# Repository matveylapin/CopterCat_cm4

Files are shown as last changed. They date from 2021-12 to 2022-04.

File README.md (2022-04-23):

# CopterCat_cm4

Полётный контроллер для стандарта FMU-v6u. Обычно на дронах для программирования устанавливают полётный контроллер, одноплатный компьютер и иногда arduino. Почему бы не объединить это в одну плату (ну или компактный стек), это уменьшит габариты и вес. В качестве arduino мы выбрали чип ESP32, это позволит организовывать из нескольких подобных плат одну независимую сеть для коммуникации между дронами.

## Спецификация 

### FMU
* STM32H753IIK6 480Mhz Cortex-M7
* 2Mb + 256Kb FLASH
* 1Mb RAM
* ICM20602, ICM42605, BMI088, BMP388, BMM150
* Полностью совместима со стандартом FMU-v6u
### Raspberry Pi
* Поддержка платы RPi CM4 
* Слот для SD-карты
* Возможность прошивки встроенной eMMC
* CAT24C256 EEPROM
* Поддержка 2 камер(CAM0-две линия, CAM1-четыре линии)
* Поддержка USB-OTG
### ESP32
* 16MB внешней FLASH (W25Q128JVS)
* 8MB внешней PSRAM (LY68L6400SLIT)
* Встроенная антенна
* USB-TTL конвертор
### Остальное
* USB-HUB USB2514B
* USB-PD с физическим переключением
* Связь ESP32 и STM32 через UART
* 3 варианта питания
* 4 универсальных GPIO от ESP32
* USB Type-C
* Размеры 40x55 мм, плата 4 слоя
___

## Разьёмы и перемычки
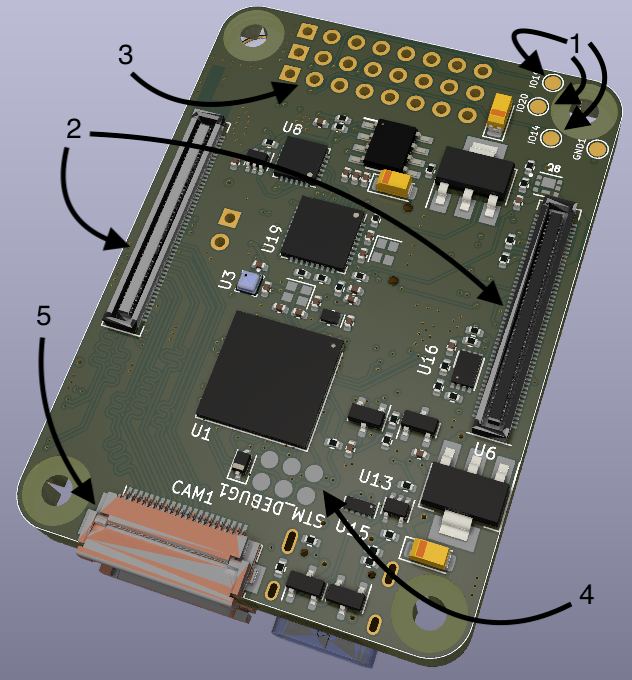
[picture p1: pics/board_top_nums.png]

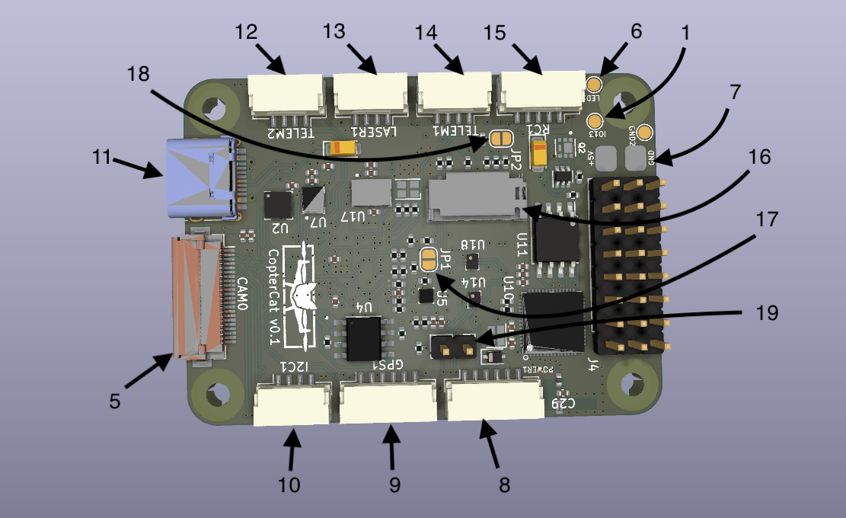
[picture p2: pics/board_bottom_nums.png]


1. GPIO ESP32 4 порта ввода вывода для подключения внешнего оборудования
2. Коннекторы RPi CM4
3. Выводы ESC 8 шт
4. Контакты программирования и отладки JTAG STM32
5. Коннекторы камер (шлейф 22 контакта с 0.5 мм расстояния между проводниками)
6. Контакт подключения адресной ленты
7. Контакты основного питания 5В
8. JST-6 стандартного шлейфа питания PX4 
9. JST-6 GPS+компас+5В
10. JST-4 I2C+5В
11. USB Type-C
12. JST-4 UART7+5В
13. JST-4 I2C RPi+3.3B для подключения дальномера
14. JST-4 UART5+5В
15. JST-5 Стандартный разъём для подключения приёмника управления
16. Слот SD карты (для RPi)
17. Джампер BOOT для STM32
18. Джампер RPIBOOT для прошивки eMMC модуля RPi CM4
19. Джампер переключения режима работы USB разъёма (при замкнутой перемычке, USB работает как вход HUB и при подключении к компьютеру будут отборажаться STM32, ESP32 и RPi CM4 в режиме OTG; при разомкнутой перемычке, USB будет работать для подключения внешних устройств к RPi, например стерео-камеры)
___

## Загрузка прошивки
### FMU
При первом запуске, в микроконтреллер придётся загрузить PX4-bootloader через порт JTAG. Подробная инструкция [здесь](https://docs.px4.io/master/en/software_update/stm32_bootloader.html#stm32-bootloader).

Для подключения к компьютеру:
1. Замкните перемычку 19
2. Подключите USB Type-C к компьютеру
3. Устройство должно появиться в [QGC](http://qgroundcontrol.com)

Также прошивку можно произвести через RPi:
1. Установите RPi CM4 в коннектор на плате
2. Разомкните перемычку 19
3. Устройство появиться в папке /dev на RPi

### ESP32
Написать программу можно либо в [Arduino IDE](https://www.arduino.cc/en/software), либо в [VS Code](https://code.visualstudio.com) с плагином [esp-idf](https://habr.com/ru/post/530638/). Далее скомпилировать и загрузить в микроконтроллер. Загрузить можно двумя способами.

С компьютера:
1. Замкните перемычку 19
2. В подключённых устройствах появиться CP2104
3. Загрузите прошивку в соотвествии с инструкцией к выбранной IDE

С RPi CM4:
1. Установите RPi CM4 в коннектор на плате
2. Разомкните перемычку 19
3. Скомпилируйте ваш код в .bin формат
4. Загрузите полученный файл на RPi
5. Загрузите прошивку в микроконтроллер с помощью esptool.py ([описание+установка](https://docs.espressif.com/projects/esptool/en/latest/esp32/index.html))

Так же ESP32 подключен к STM32 по UART, это позволит связывть между собой не просто RPi, а сразу FMU.

### RPi CM4
Слот SD карты работает как на стандартной RPi. Для плат с eMMC порядок загрузки операционной системы не отличается от CM4 IO Board ([инструкция](https://www.jeffgeerling.com/blog/2020/how-flash-raspberry-pi-os-compute-module-4-emmc-usbboot)).

___

## Общая информация
* Все требуемые для заказа файлы находится в папке /gerbers.
* Проект выполнен в программе [KiCAD v6](https://www.kicad.org)
* Библиотеки компонентов взяты с сайта [snapeda](https://www.snapeda.com)

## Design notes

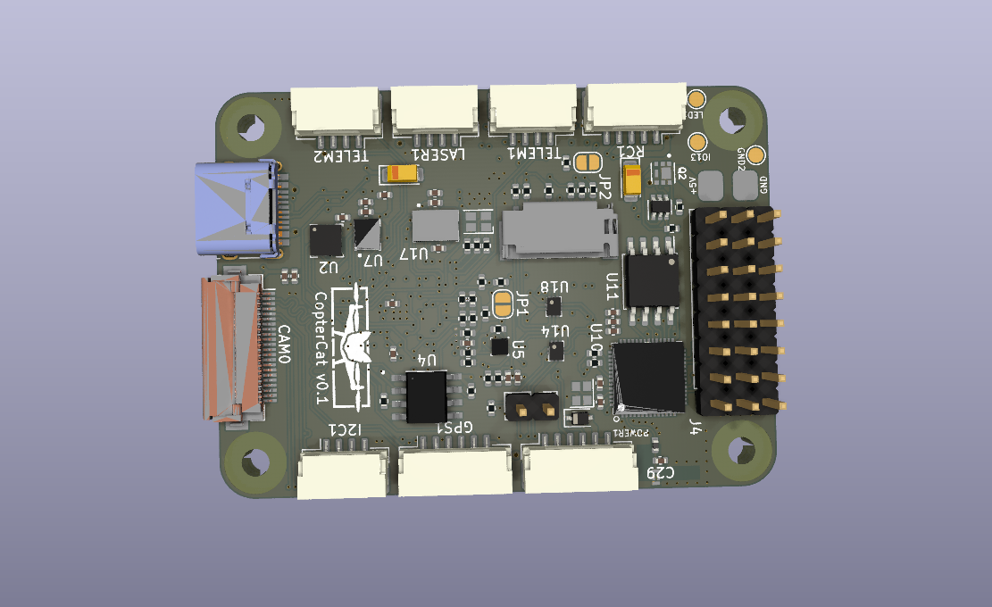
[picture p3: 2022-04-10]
pics/board_bottom.png

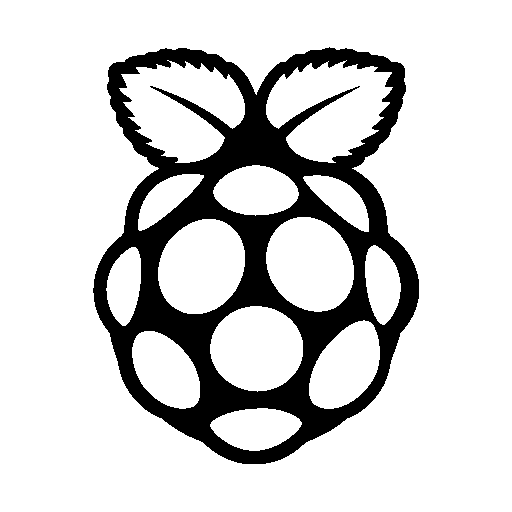
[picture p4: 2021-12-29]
pics/raspberry-pi-4-599381.bmp

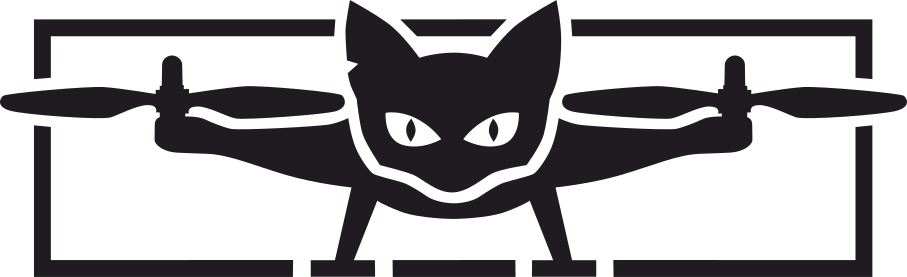
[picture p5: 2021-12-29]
pics/котокоптер лого.png

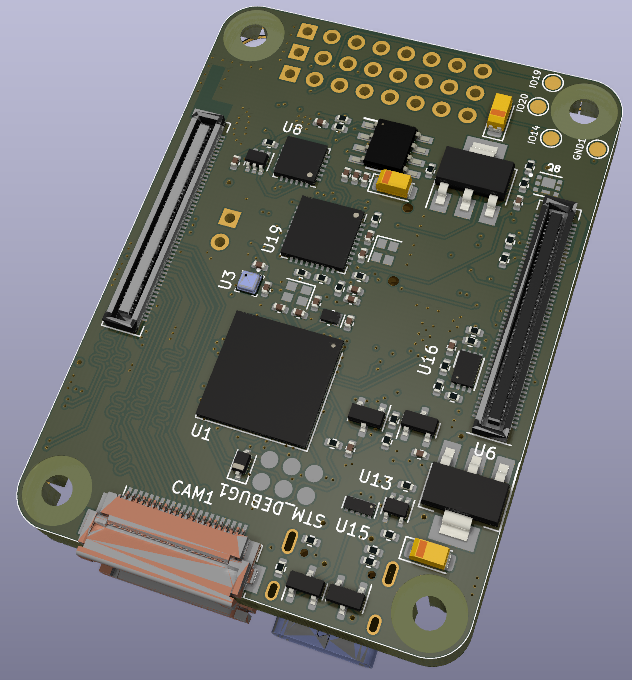
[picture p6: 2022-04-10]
pics/board_top.png

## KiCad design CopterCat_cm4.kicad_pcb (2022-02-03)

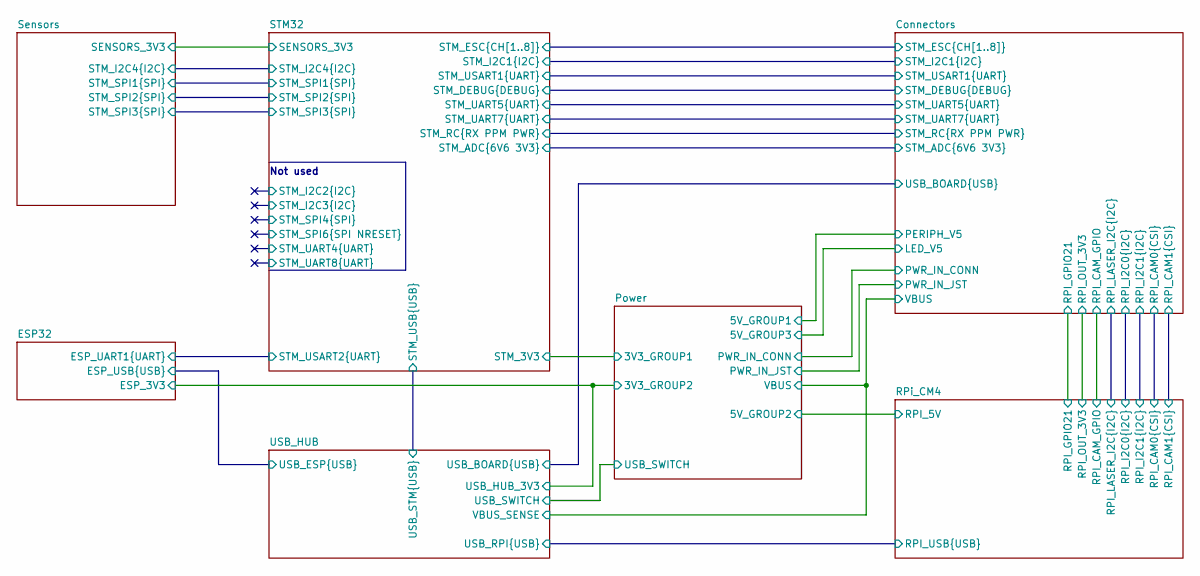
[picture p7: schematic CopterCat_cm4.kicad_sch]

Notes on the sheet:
Not used

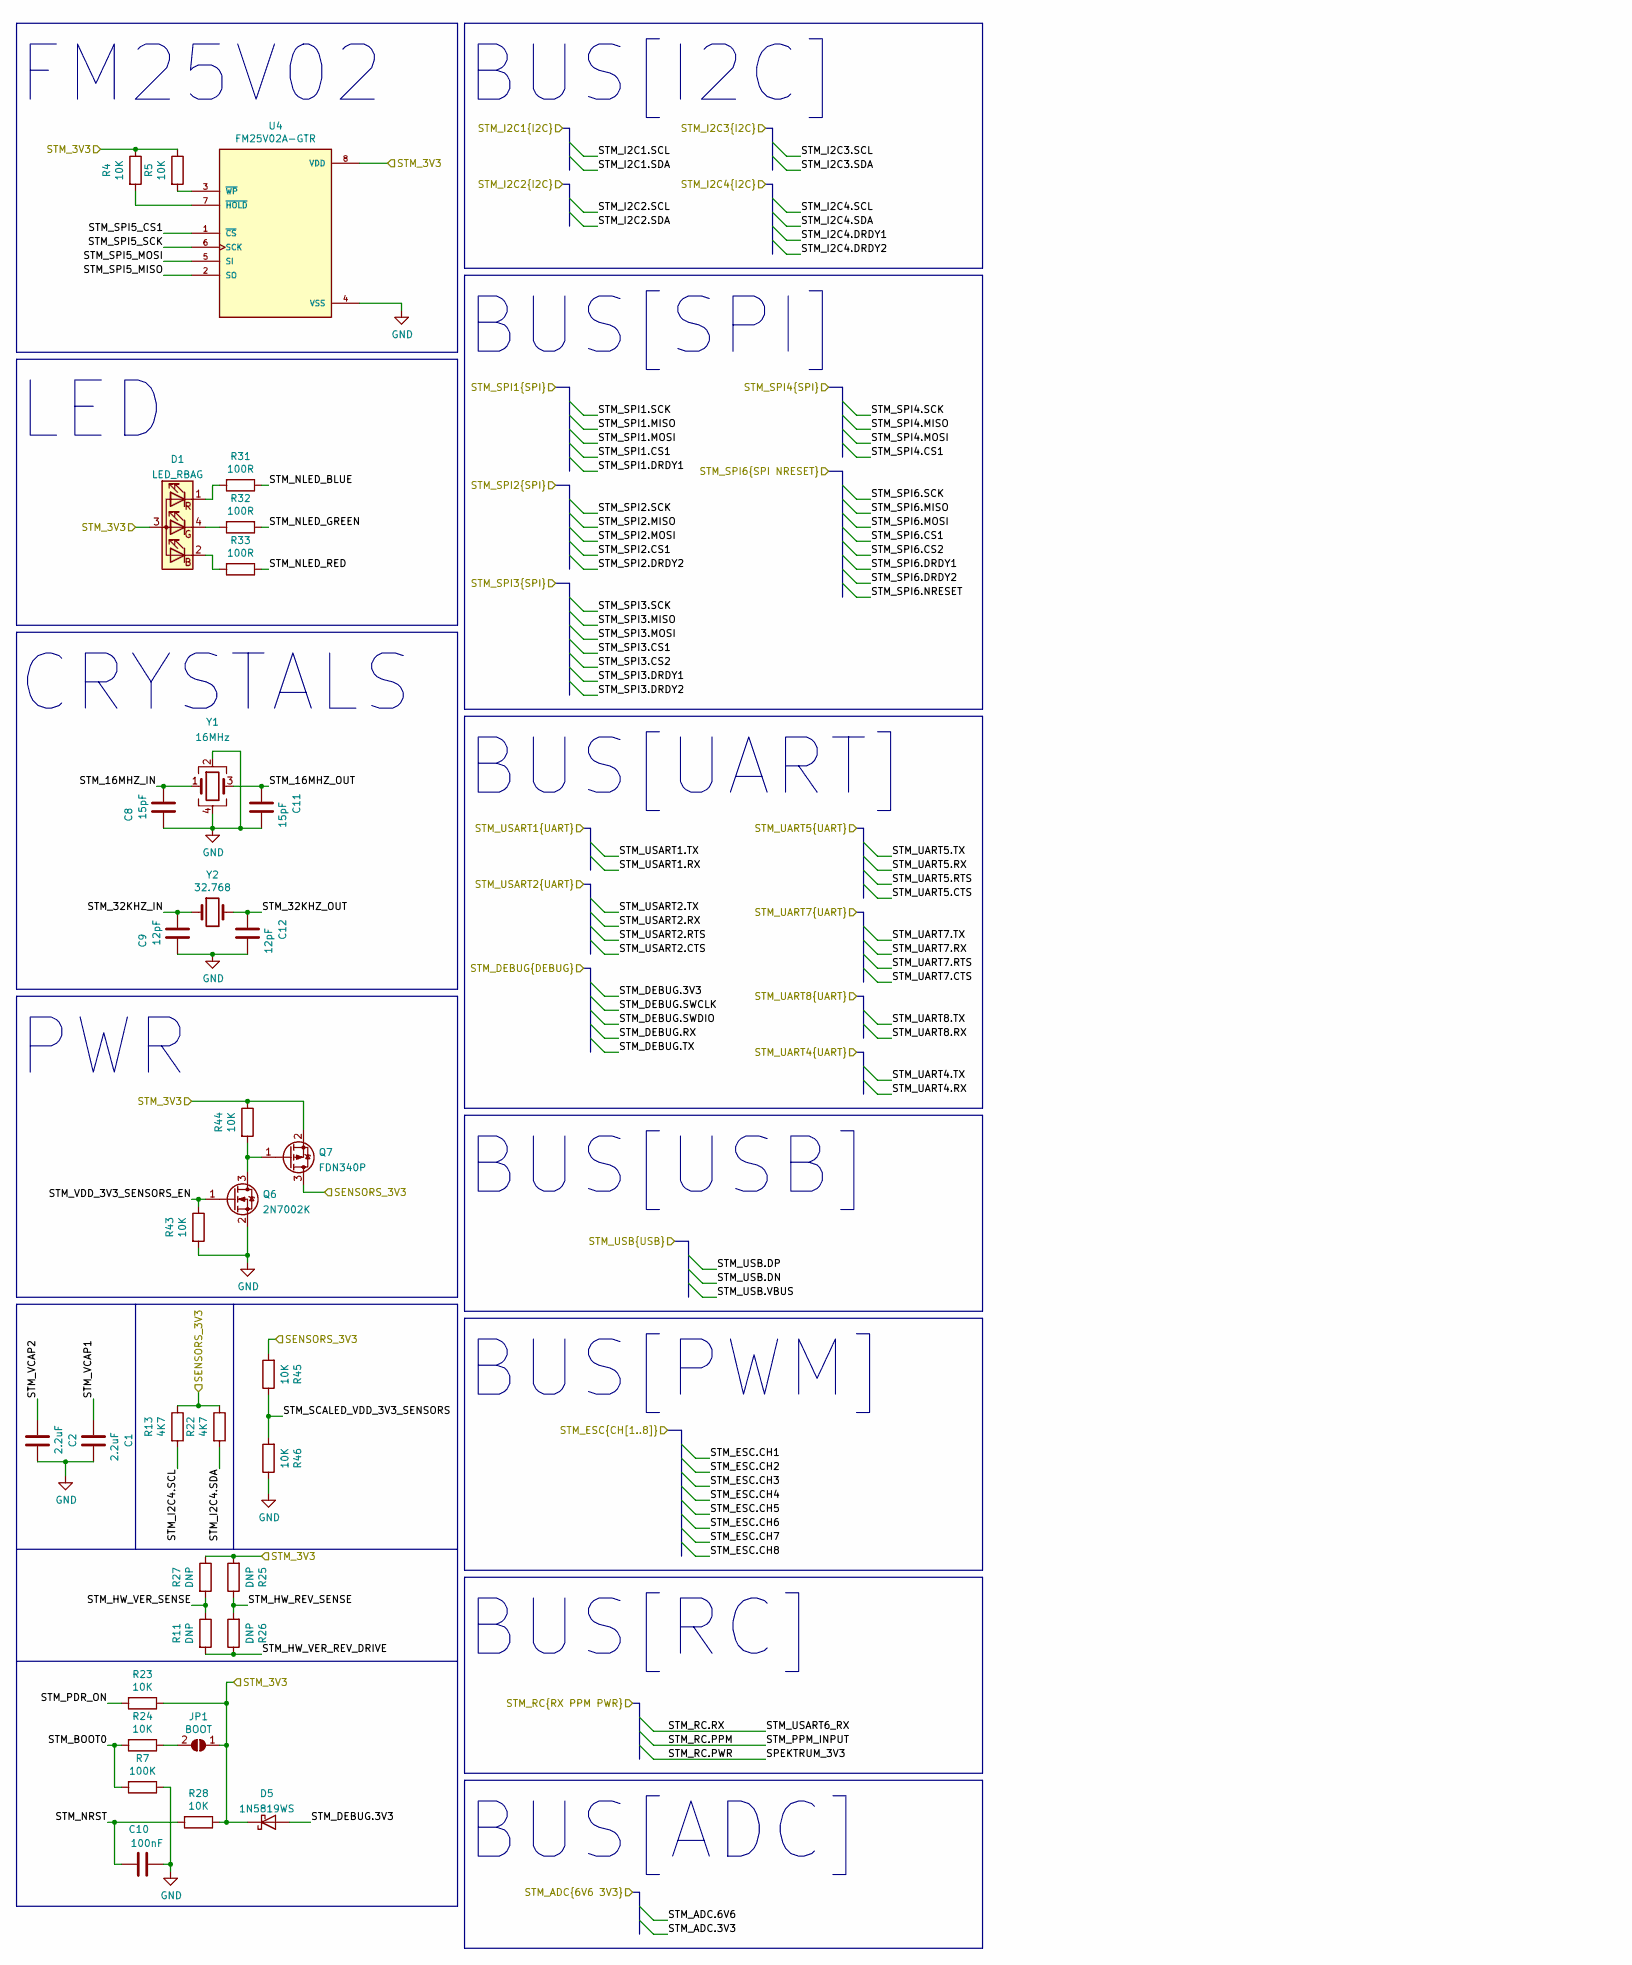
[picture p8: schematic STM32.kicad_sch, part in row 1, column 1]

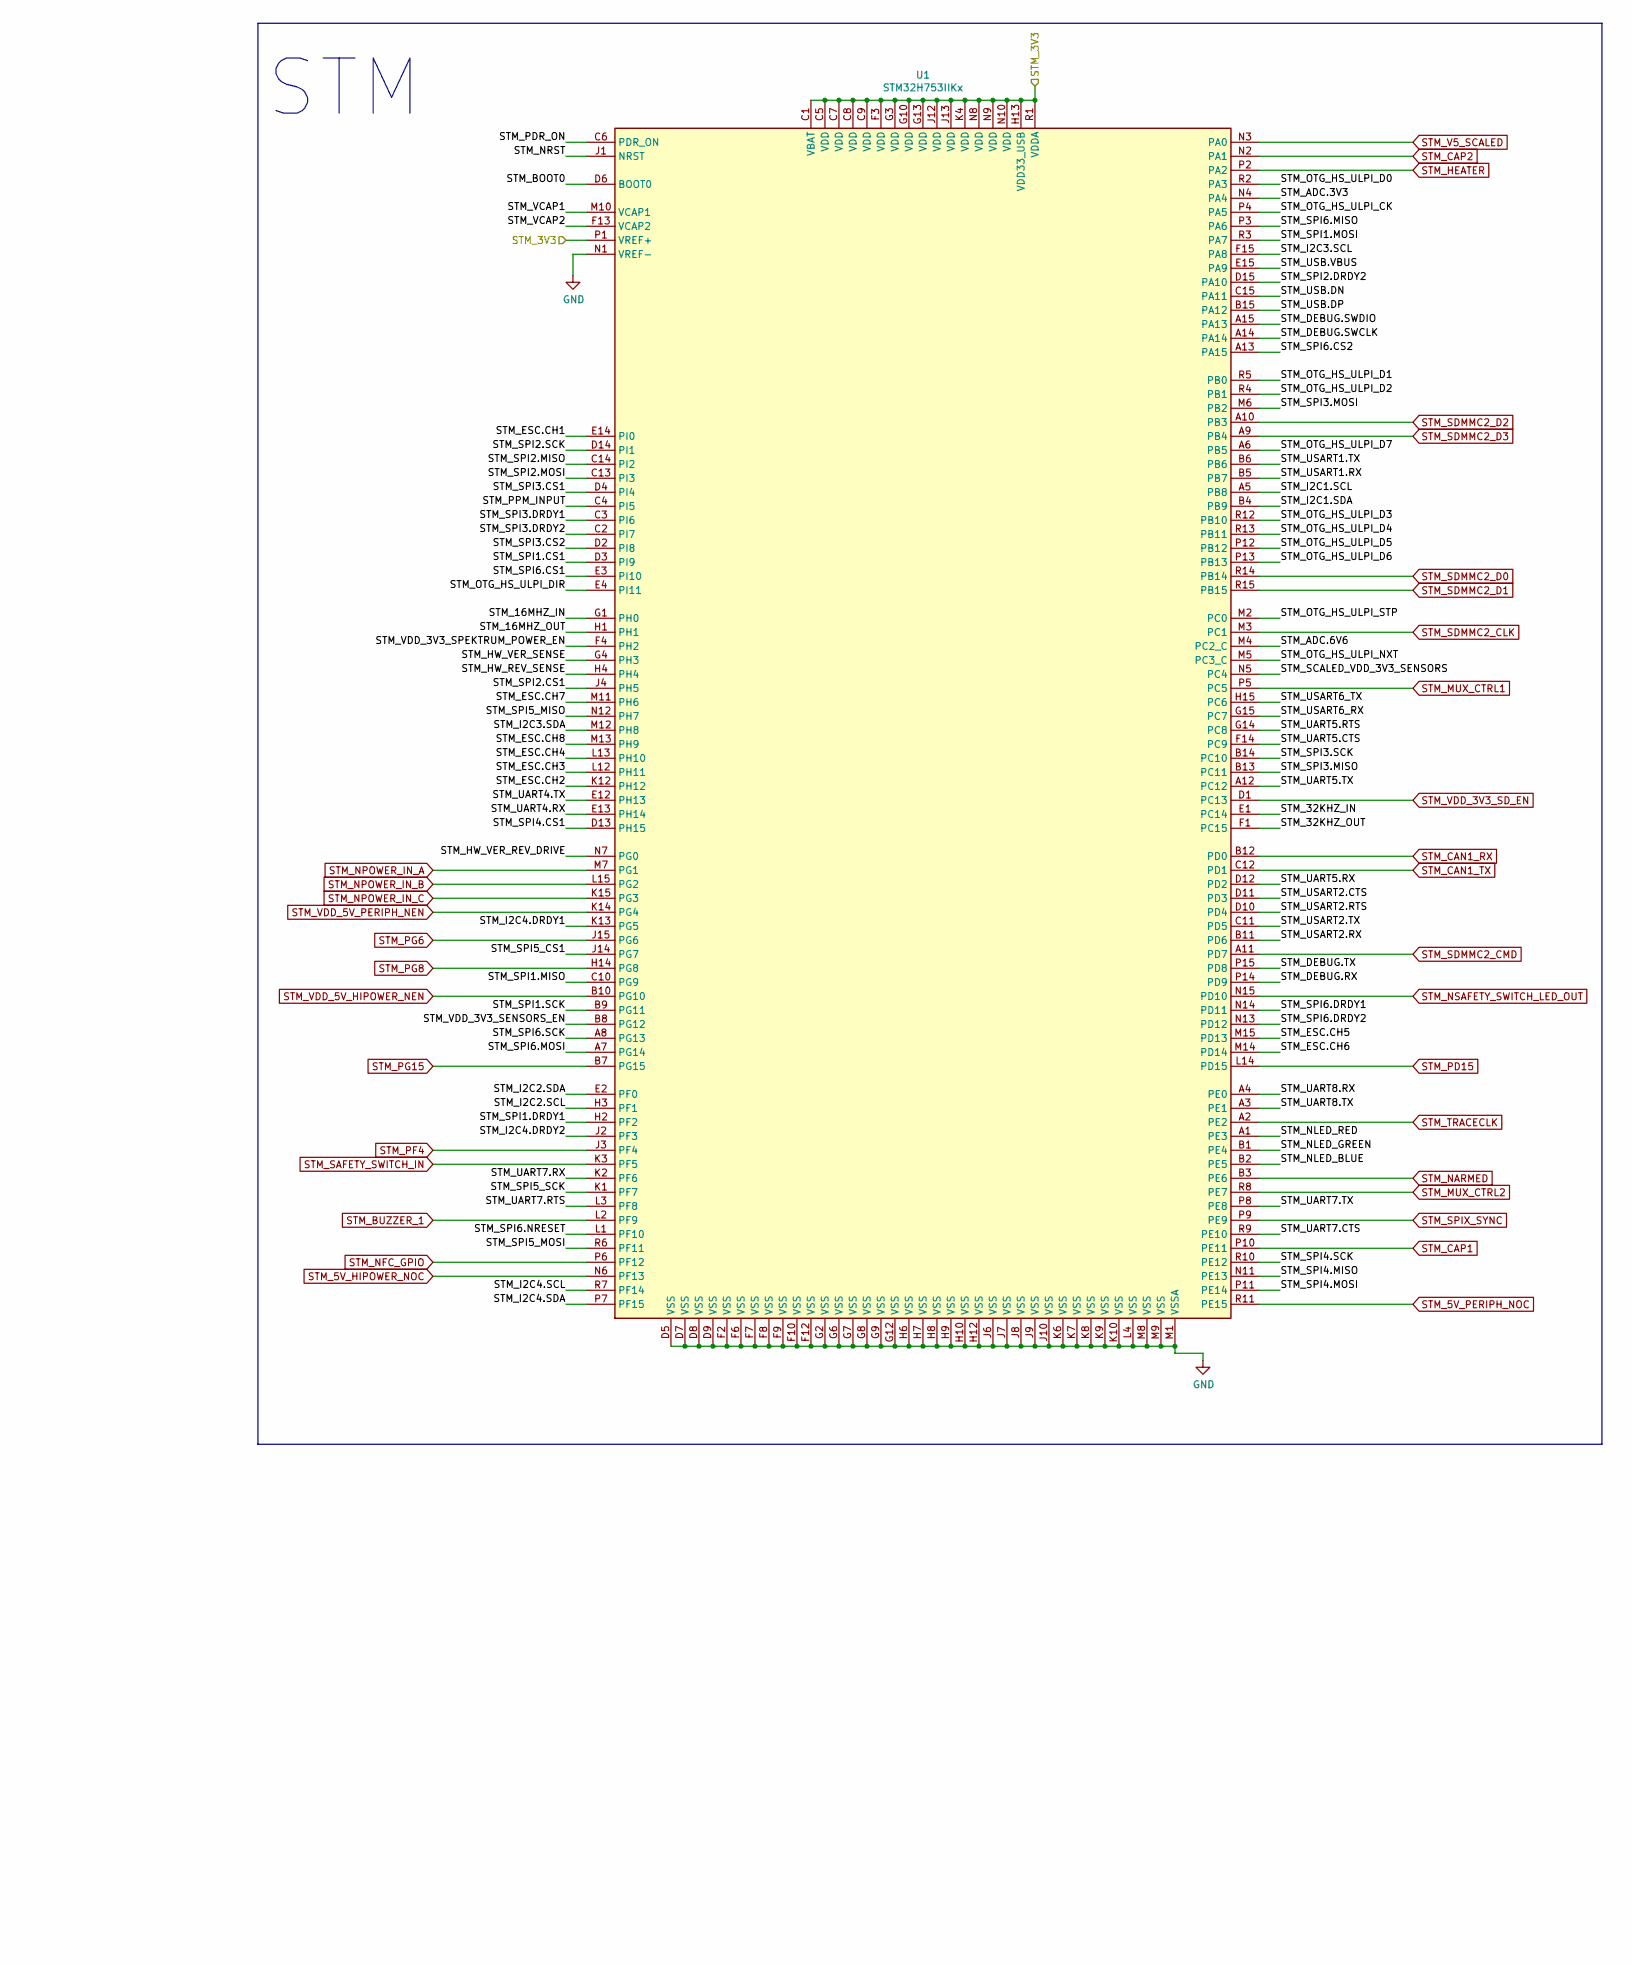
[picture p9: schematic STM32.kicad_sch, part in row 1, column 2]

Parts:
C1, C2: 2.2uF; C_0402_1005Metric
C8, C11: 15pF; C_0402_1005Metric
C9, C12: 12pF; C_0402_1005Metric
C10: 100nF; C_0402_1005Metric
D1: LED_RBAG; LED_Cree-PLCC4_2x2mm_CW; Manufacturer_Part_Number FM-B2020RGBA-HG
D5: 1N5819WS; D_SOD-323; Manufacturer_Part_Number 1N5819WS
JP1: BOOT; SolderJumper-2_P1.3mm_Open_TrianglePad1.0x1.5mm
Q6: 2N7002K; SOT-23; Manufacturer_Part_Number 2N7002,215
Q7: FDN340P; SOT-23; Manufacturer_Part_Number FDN340P
R4, R5, R23, R24, R28, R43, R44, R45, R46: 10K; R_0402_1005Metric
R7: 100K; R_0402_1005Metric
R11, R25, R26, R27: DNP; R_0402_1005Metric
R13, R22: 4K7; R_0402_1005Metric
R31, R32, R33: 100R; R_0402_1005Metric
U1: STM32H753IIKx; UFBGA-201_10x10mm_Layout15x15_P0.65mm; Manufacturer_Part_Number STM32H753IIK6
U4: FM25V02A-GTR; SOIC127P602X172-8N; Manufacturer_Part_Number FM25V02A-GTR
Y1: 16MHz; Crystal_SMD_2016-4Pin_2.0x1.6mm; Manufacturer_Part_Number OT201616MJBA4SL
Y2: 32.768; Crystal_SMD_MicroCrystal_CM9V-T1A-2Pin_1.6x1.0mm; Manufacturer_Part_Number SC-16S

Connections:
/Connectors/STM_ADC.3V3: U1.N4 (PA4); also elsewhere on the board
/Connectors/STM_ADC.6V6: U1.M4 (PC2_C); also elsewhere on the board
/Connectors/STM_DEBUG.3V3: D5.2 (A); also elsewhere on the board
/Connectors/STM_DEBUG.RX: U1.P14 (PD9); also elsewhere on the board
/Connectors/STM_DEBUG.SWCLK: U1.A14; also elsewhere on the board
/Connectors/STM_DEBUG.SWDIO: U1.A15 (PA13); also elsewhere on the board
/Connectors/STM_DEBUG.TX: U1.P15 (PD8); also elsewhere on the board
/Connectors/STM_ESC.CH1: U1.E14 (PI0); also elsewhere on the board
/Connectors/STM_ESC.CH2: U1.K12 (PH12); also elsewhere on the board
/Connectors/STM_ESC.CH3: U1.L12 (PH11); also elsewhere on the board
/Connectors/STM_ESC.CH4: U1.L13 (PH10); also elsewhere on the board
/Connectors/STM_ESC.CH5: U1.M15 (PD13); also elsewhere on the board
/Connectors/STM_ESC.CH6: U1.M14 (PD14); also elsewhere on the board
/Connectors/STM_ESC.CH7: U1.M11 (PH6); also elsewhere on the board
/Connectors/STM_ESC.CH8: U1.M13 (PH9); also elsewhere on the board
/Connectors/STM_I2C1.SCL: U1.A5 (PB8); also elsewhere on the board
/Connectors/STM_I2C1.SDA: U1.B4 (PB9); also elsewhere on the board
/Connectors/STM_RC.PPM: U1.C4 (PI5); also elsewhere on the board
/Connectors/STM_RC.RX: U1.G15 (PC7); also elsewhere on the board
/Connectors/STM_UART5.CTS: U1.F14 (PC9)
/Connectors/STM_UART5.RTS: U1.G14 (PC8)
/Connectors/STM_UART5.RX: U1.D12 (PD2); also elsewhere on the board
/Connectors/STM_UART5.TX: U1.A12 (PC12); also elsewhere on the board
/Connectors/STM_UART7.CTS: U1.R9 (PE10)
/Connectors/STM_UART7.RTS: U1.L3 (PF8)
/Connectors/STM_UART7.RX: U1.K2 (PF6); also elsewhere on the board
/Connectors/STM_UART7.TX: U1.P8 (PE8); also elsewhere on the board
/Connectors/STM_USART1.RX: U1.B5 (PB7); also elsewhere on the board
/Connectors/STM_USART1.TX: U1.B6; also elsewhere on the board
/ESP32/ESP_UART1.CTS: U1.D11 (PD3)
/ESP32/ESP_UART1.RTS: U1.D10 (PD4)
/ESP32/ESP_UART1.RX: U1.B11 (PD6); also elsewhere on the board
/ESP32/ESP_UART1.TX: U1.C11 (PD5); also elsewhere on the board
/Power/3V3_GROUP1: D1.3 (A), D5.1 (K), JP1.1 (A), Q7.2 (S), R4.1, R5.1, R23.1, R25.2, R27.1, R28.1, R44.1, U1.C1 (VBAT), U1.C5 (VDD), U1.C7 (VDD), U1.C8 (VDD), U1.C9 (VDD), U1.F3 (VDD), U1.G3 (VDD), U1.G10 (VDD), U1.G13 (VDD), U1.H13 (VDD33_USB), U1.J12 (VDD), U1.J13 (VDD), U1.K4 (VDD), U1.N8 (VDD), U1.N9 (VDD), U1.N10 (VDD), U1.P1 (VREF+), U1.R1 (VDDA), U4.8 (VDD); also elsewhere on the board
/STM32/SENSORS_3V3: Q7.3 (D), R13.1, R22.1, R45.2; also elsewhere on the board
/STM32/STM_16MHZ_IN: C8.2, U1.G1 (PH0), Y1.1
/STM32/STM_16MHZ_OUT: C11.1, U1.H1, Y1.3
/STM32/STM_32KHZ_IN: C9.2, U1.E1 (PC14), Y2.1
/STM32/STM_32KHZ_OUT: C12.1, U1.F1 (PC15), Y2.2
/STM32/STM_BOOT0: R7.2, R24.2, U1.D6 (BOOT0)
/STM32/STM_HW_REV_SENSE: R25.1, R26.2, U1.H4
/STM32/STM_HW_VER_REV_DRIVE: R11.2, R26.1, U1.N7 (PG0)
/STM32/STM_HW_VER_SENSE: R11.1, R27.2, U1.G4 (PH3)
/STM32/STM_I2C2.SCL: U1.H3 (PF1)
/STM32/STM_I2C2.SDA: U1.E2 (PF0)
/STM32/STM_I2C3.SCL: U1.F15 (PA8)
/STM32/STM_I2C3.SDA: U1.M12 (PH8)
/STM32/STM_I2C4.DRDY1: U1.K13 (PG5); also elsewhere on the board
/STM32/STM_I2C4.DRDY2: U1.J2 (PF3); also elsewhere on the board
/STM32/STM_I2C4.SCL: R13.2, U1.R7 (PF14); also elsewhere on the board
/STM32/STM_I2C4.SDA: R22.2, U1.P7 (PF15); also elsewhere on the board
/STM32/STM_NLED_BLUE: R31.1, U1.B2 (PE5)
/STM32/STM_NLED_GREEN: R32.2, U1.B1 (PE4)
/STM32/STM_NLED_RED: R33.1, U1.A1 (PE3)
/STM32/STM_NRST: C10.1, R28.2, U1.J1 (NRST)
/STM32/STM_OTG_HS_ULPI_CK: U1.P4 (PA5)
/STM32/STM_OTG_HS_ULPI_D0: U1.R2 (PA3)
/STM32/STM_OTG_HS_ULPI_D1: U1.R5 (PB0)
/STM32/STM_OTG_HS_ULPI_D2: U1.R4 (PB1)
/STM32/STM_OTG_HS_ULPI_D3: U1.R12 (PB10)
/STM32/STM_OTG_HS_ULPI_D4: U1.R13 (PB11)
/STM32/STM_OTG_HS_ULPI_D5: U1.P12 (PB12)
/STM32/STM_OTG_HS_ULPI_D6: U1.P13 (PB13)
/STM32/STM_OTG_HS_ULPI_D7: U1.A6 (PB5)
/STM32/STM_OTG_HS_ULPI_DIR: U1.E4 (PI11)
/STM32/STM_OTG_HS_ULPI_NXT: U1.M5 (PC3_C)
/STM32/STM_OTG_HS_ULPI_STP: U1.M2 (PC0)
/STM32/STM_PDR_ON: R23.2, U1.C6 (PDR_ON)
/STM32/STM_SCALED_VDD_3V3_SENSORS: R45.1, R46.2, U1.N5 (PC4)
/STM32/STM_SPI1.CS1: U1.D3 (PI9); also elsewhere on the board
/STM32/STM_SPI1.DRDY1: U1.H2 (PF2); also elsewhere on the board
/STM32/STM_SPI1.MISO: U1.C10 (PG9); also elsewhere on the board
/STM32/STM_SPI1.MOSI: U1.R3 (PA7); also elsewhere on the board
/STM32/STM_SPI1.SCK: U1.B9 (PG11); also elsewhere on the board
/STM32/STM_SPI2.CS1: U1.J4 (PH5); also elsewhere on the board
/STM32/STM_SPI2.DRDY2: U1.D15 (PA10); also elsewhere on the board
/STM32/STM_SPI2.MISO: U1.C14 (PI2); also elsewhere on the board
/STM32/STM_SPI2.MOSI: U1.C13 (PI3); also elsewhere on the board
/STM32/STM_SPI2.SCK: U1.D14 (PI1); also elsewhere on the board
/STM32/STM_SPI3.CS1: U1.D4 (PI4); also elsewhere on the board
/STM32/STM_SPI3.CS2: U1.D2 (PI8); also elsewhere on the board
/STM32/STM_SPI3.DRDY1: U1.C3 (PI6); also elsewhere on the board
/STM32/STM_SPI3.DRDY2: U1.C2 (PI7); also elsewhere on the board
/STM32/STM_SPI3.MISO: U1.B13 (PC11); also elsewhere on the board
/STM32/STM_SPI3.MOSI: U1.M6 (PB2); also elsewhere on the board
/STM32/STM_SPI3.SCK: U1.B14 (PC10); also elsewhere on the board
/STM32/STM_SPI4.CS1: U1.D13 (PH15)
/STM32/STM_SPI4.MISO: U1.N11 (PE13)
/STM32/STM_SPI4.MOSI: U1.P11 (PE14)
/STM32/STM_SPI4.SCK: U1.R10 (PE12)
/STM32/STM_SPI5_CS1: U1.J14 (PG7), U4.1 (~CS)
/STM32/STM_SPI5_MISO: U1.N12 (PH7), U4.2 (SO)
/STM32/STM_SPI5_MOSI: U1.R6 (PF11), U4.5 (SI)
/STM32/STM_SPI5_SCK: U1.K1 (PF7), U4.6 (SCK)
/STM32/STM_SPI6.CS1: U1.E3 (PI10)
/STM32/STM_SPI6.CS2: U1.A13 (PA15)
/STM32/STM_SPI6.DRDY1: U1.N14 (PD11)
/STM32/STM_SPI6.DRDY2: U1.N13 (PD12)
/STM32/STM_SPI6.MISO: U1.P3 (PA6)
/STM32/STM_SPI6.MOSI: U1.A7 (PG14)
/STM32/STM_SPI6.NRESET: U1.L1 (PF10)
/STM32/STM_SPI6.SCK: U1.A8 (PG13)
/STM32/STM_UART4.RX: U1.E13 (PH14)
/STM32/STM_UART4.TX: U1.E12 (PH13)
/STM32/STM_UART8.RX: U1.A4 (PE0)
/STM32/STM_UART8.TX: U1.A3 (PE1)
/STM32/STM_USART6_TX: U1.H15 (PC6)
/STM32/STM_USB.DN: U1.C15 (PA11); also elsewhere on the board
/STM32/STM_USB.DP: U1.B15 (PA12); also elsewhere on the board
/STM32/STM_USB.VBUS: U1.E15 (PA9); also elsewhere on the board
/STM32/STM_VCAP1: C1.1, U1.M10 (VCAP1)
/STM32/STM_VCAP2: C2.1, U1.F13 (VCAP2)
/STM32/STM_VDD_3V3_SENSORS_EN: Q6.1 (G), R43.1, U1.B8 (PG12)
/STM32/STM_VDD_3V3_SPEKTRUM_POWER_EN: U1.F4 (PH2)
GND: C1.2, C2.2, C8.1, C9.1, C10.2, C11.2, C12.2, Q6.2 (S), R7.1, R43.2, R46.1, U1.D5 (VSS), U1.D7 (VSS), U1.D8 (VSS), U1.D9 (VSS), U1.F2 (VSS), U1.F6 (VSS), U1.F7 (VSS), U1.F8 (VSS), U1.F9 (VSS), U1.F10 (VSS), U1.F12 (VSS), U1.G2 (VSS), U1.G6 (VSS), U1.G7 (VSS), U1.G8 (VSS), U1.G9 (VSS), U1.G12 (VSS), U1.H6 (VSS), U1.H7 (VSS), U1.H8 (VSS), U1.H9 (VSS), U1.H10 (VSS), U1.H12 (VSS), U1.J6 (VSS), U1.J7 (VSS), U1.J8 (VSS), U1.J9 (VSS), U1.J10 (VSS), U1.K6 (VSS), U1.K7 (VSS), U1.K8 (VSS), U1.K9 (VSS), U1.K10 (VSS), U1.L4 (VSS), U1.M1 (VSSA), U1.M8 (VSS), U1.M9 (VSS), U1.N1 (VREF-), U4.4 (VSS), Y1.2, Y1.4; also elsewhere on the board
unnamed: D1.1 (RK), R31.2
unnamed: D1.2 (BK), R33.2
unnamed: D1.4 (GK), R32.1
unnamed: JP1.2 (B), R24.1
unnamed: Q6.3 (D), Q7.1 (G), R44.2
unnamed: R4.2, U4.7 (~HOLD)
unnamed: R5.2, U4.3 (~WP)
STM_5V_HIPOWER_NOC: U1.N6 (PF13)
STM_5V_PERIPH_NOC: U1.R11 (PE15)
STM_BUZZER_1: U1.L2 (PF9)
STM_CAN1_RX: U1.B12 (PD0)
STM_CAN1_TX: U1.C12 (PD1)
STM_CAP1: U1.P10 (PE11)
STM_CAP2: U1.N2 (PA1)
STM_HEATER: U1.P2 (PA2)
STM_MUX_CTRL1: U1.P5 (PC5)
STM_MUX_CTRL2: U1.R8 (PE7)
STM_NARMED: U1.B3 (PE6)
STM_NFC_GPIO: U1.P6 (PF12)
STM_NPOWER_IN_A: U1.M7 (PG1)
STM_NPOWER_IN_B: U1.L15 (PG2)
STM_NPOWER_IN_C: U1.K15 (PG3)
STM_NSAFETY_SWITCH_LED_OUT: U1.N15 (PD10)
STM_PD15: U1.L14 (PD15)
STM_PF4: U1.J3 (PF4)
STM_PG6: U1.J15 (PG6)
STM_PG8: U1.H14 (PG8)
STM_PG15: U1.B7 (PG15)
STM_SAFETY_SWITCH_IN: U1.K3 (PF5)
STM_SDMMC2_CLK: U1.M3 (PC1)
STM_SDMMC2_CMD: U1.A11 (PD7)
STM_SDMMC2_D0: U1.R14 (PB14)
STM_SDMMC2_D1: U1.R15 (PB15)
STM_SDMMC2_D2: U1.A10 (PB3)
STM_SDMMC2_D3: U1.A9 (PB4)
STM_SPIX_SYNC: U1.P9 (PE9)
STM_TRACECLK: U1.A2 (PE2)
STM_V5_SCALED: U1.N3 (PA0)
STM_VDD_3V3_SD_EN: U1.D1 (PC13)
STM_VDD_5V_HIPOWER_NEN: U1.B10 (PG10)
STM_VDD_5V_PERIPH_NEN: U1.K14 (PG4)

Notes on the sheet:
BUS[RC]
BUS[SPI]
PWR
BUS[UART]
CRYSTALS
FM25V02
BUS[USB]
STM
BUS[ADC]
LED
BUS[PWM]
BUS[I2C]

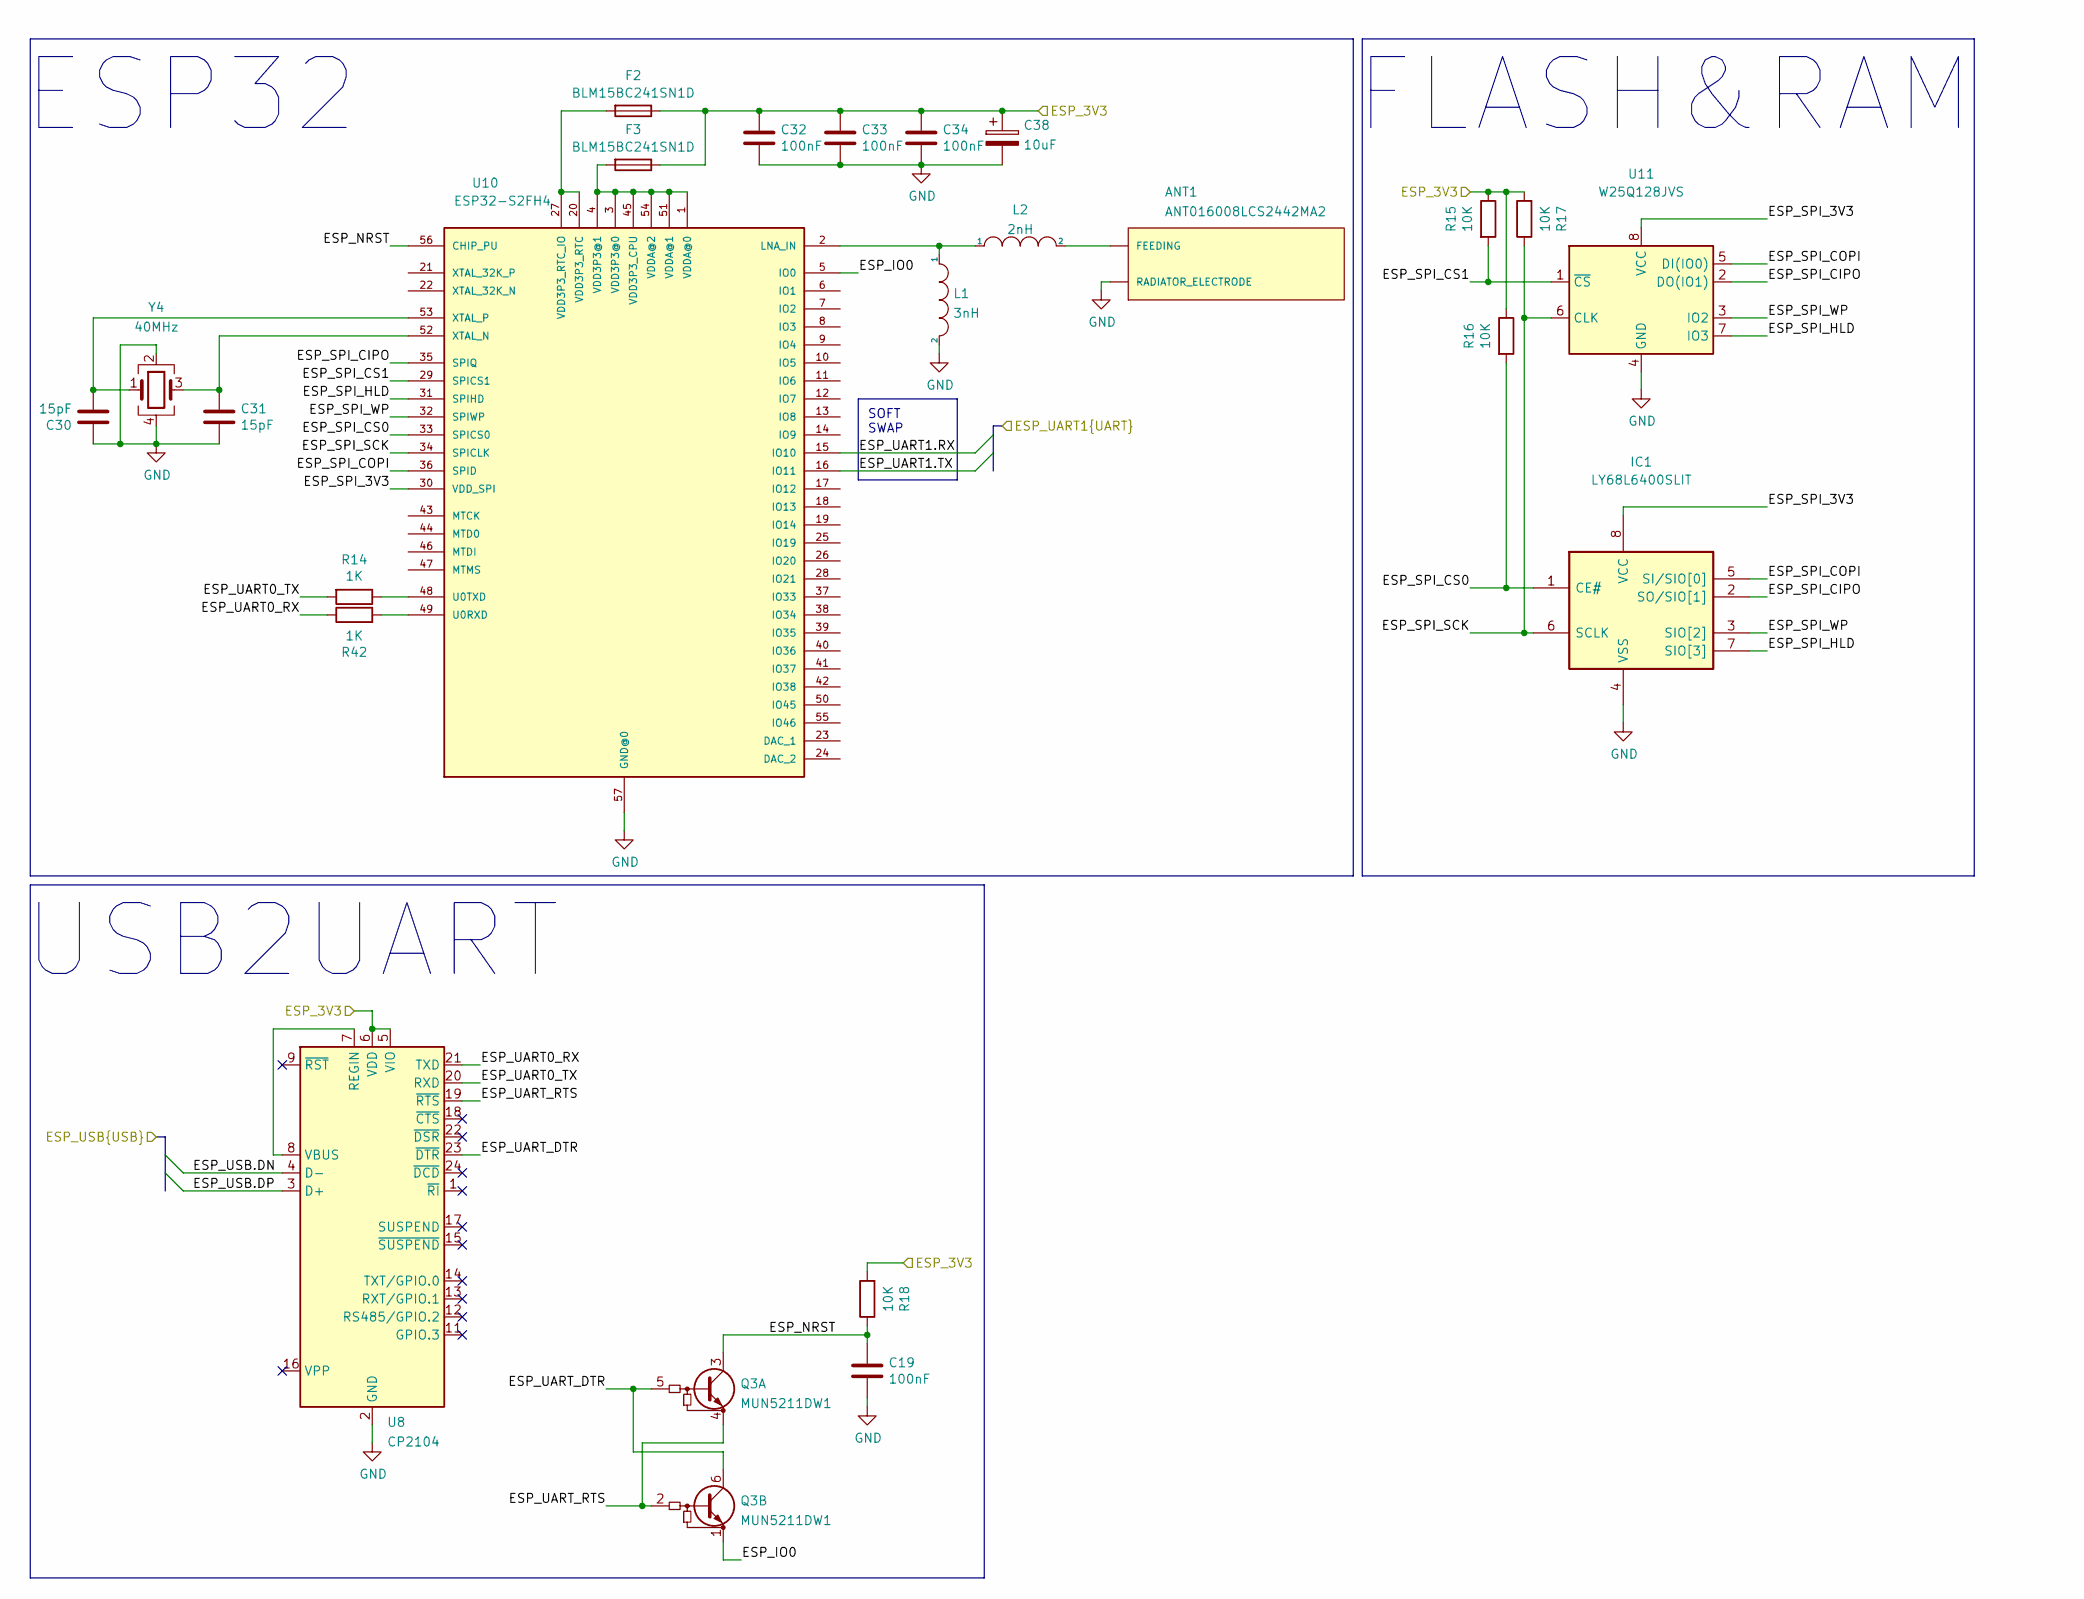
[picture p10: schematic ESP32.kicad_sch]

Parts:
ANT1: ANT016008LCS2442MA2; ANT_ANT016008LCS2442MA2; Manufacturer_Part_Number ANT016008LCS2442MA2
C19, C32, C33, C34: 100nF; C_0402_1005Metric
C30, C31: 15pF; C_0402_1005Metric
C38: 10uF; CP_EIA-3216-18_Kemet-A; Manufacturer_Part_Number CL31A226KAHNNNE
F2, F3: BLM15BC241SN1D; Fuse_0402_1005Metric; Manufacturer_Part_Number BLM15BC241SN1D
IC1: LY68L6400SLIT; SOIC127P600X175-8N; Manufacturer_Part_Number LY68L6400SLIT
L1: 3nH; L_0402_1005Metric; Manufacturer_Part_Number SDCL1005C2N0STDF
L2: 2nH; L_0402_1005Metric; Manufacturer_Part_Number SDCL1005C2N0STDF
Q3: MUN5211DW1; SOT-363_SC-70-6; Manufacturer_Part_Number MUN5211DW1T1G
R14, R42: 1K; R_0402_1005Metric
R15, R16, R17, R18: 10K; R_0402_1005Metric
U8: CP2104; QFN-24-1EP_4x4mm_P0.5mm_EP2.6x2.6mm; Manufacturer_Part_Number CP2104-F03-GMR
U10: ESP32-S2FH4; QFN40P700X700X90-57T400N; Manufacturer_Part_Number ESP32-S2FH4
U11: W25Q128JVS; SOIC-8_5.23x5.23mm_P1.27mm; Manufacturer_Part_Number W25Q128JVS
Y4: 40MHz; Crystal_SMD_2016-4Pin_2.0x1.6mm; Manufacturer_Part_Number OT201640MJBA4SL

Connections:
/ESP32/ESP_3V3: C32.1, C33.1, C34.1, C38.1, F2.1, F3.1, R15.1, R16.1, R17.2, R18.2, U8.5 (VIO), U8.6 (VDD); also elsewhere on the board
/ESP32/ESP_IO0: Q3.1 (E2), U10.5 (IO0)
/ESP32/ESP_NRST: C19.1, Q3.3 (C1), R18.1, U10.56 (CHIP_PU)
/ESP32/ESP_SPI_3V3: IC1.8 (VCC), U10.30 (VDD_SPI), U11.8 (VCC)
/ESP32/ESP_SPI_CIPO: IC1.2 (SO/SIO[1]), U10.35 (SPIQ), U11.2 (DO(IO1))
/ESP32/ESP_SPI_COPI: IC1.5 (SI/SIO[0]), U10.36 (SPID), U11.5 (DI(IO0))
/ESP32/ESP_SPI_CS0: IC1.1 (CE#), R16.2, U10.33 (SPICS0)
/ESP32/ESP_SPI_CS1: R15.2, U10.29 (SPICS1), U11.1 (~CS)
/ESP32/ESP_SPI_HLD: IC1.7 (SIO[3]), U10.31 (SPIHD), U11.7 (IO3)
/ESP32/ESP_SPI_SCK: IC1.6 (SCLK), R17.1, U10.34 (SPICLK), U11.6 (CLK)
/ESP32/ESP_SPI_WP: IC1.3 (SIO[2]), U10.32 (SPIWP), U11.3 (IO2)
/ESP32/ESP_UART0_RX: R42.1, U8.21 (TXD)
/ESP32/ESP_UART0_TX: R14.2, U8.20 (RXD)
/ESP32/ESP_UART1.RX: U10.15 (IO10); also elsewhere on the board
/ESP32/ESP_UART1.TX: U10.16 (IO11); also elsewhere on the board
/ESP32/ESP_UART_DTR: Q3.5 (B1), Q3.6 (C2), U8.23 (~DTR)
/ESP32/ESP_UART_RTS: Q3.2 (B2), Q3.4 (E1), U8.19 (~RTS)
/ESP32/ESP_USB.DN: U8.4 (D-); also elsewhere on the board
/ESP32/ESP_USB.DP: U8.3 (D+); also elsewhere on the board
GND: ANT1.1 (RADIATOR_ELECTRODE), C19.2, C30.1, C31.2, C32.2, C33.2, C34.2, C38.2, IC1.4 (VSS), L1.2, U8.2 (GND), U8.25 (GND), U10.57 (GND@0), U11.4 (GND), Y4.2, Y4.4; also elsewhere on the board
unnamed: ANT1.4 (FEEDING), L2.2
unnamed: C30.2, U10.53 (XTAL_P), Y4.1
unnamed: C31.1, U10.52 (XTAL_N), Y4.3
unnamed: F2.2, U10.20 (VDD3P3_RTC), U10.27 (VDD3P3_RTC_IO)
unnamed: F3.2, U10.1 (VDDA@0), U10.3 (VDD3P3@0), U10.4 (VDD3P3@1), U10.45 (VDD3P3_CPU), U10.51 (VDDA@1), U10.54 (VDDA@2)
unnamed: L1.1, L2.1, U10.2 (LNA_IN)
unnamed: R14.1, U10.48 (U0TXD)
unnamed: R42.2, U10.49 (U0RXD)
unnamed: U8.7 (REGIN), U8.8 (VBUS)

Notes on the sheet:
ESP32
FLASH&RAM
USB2UART
SOFT SWAP

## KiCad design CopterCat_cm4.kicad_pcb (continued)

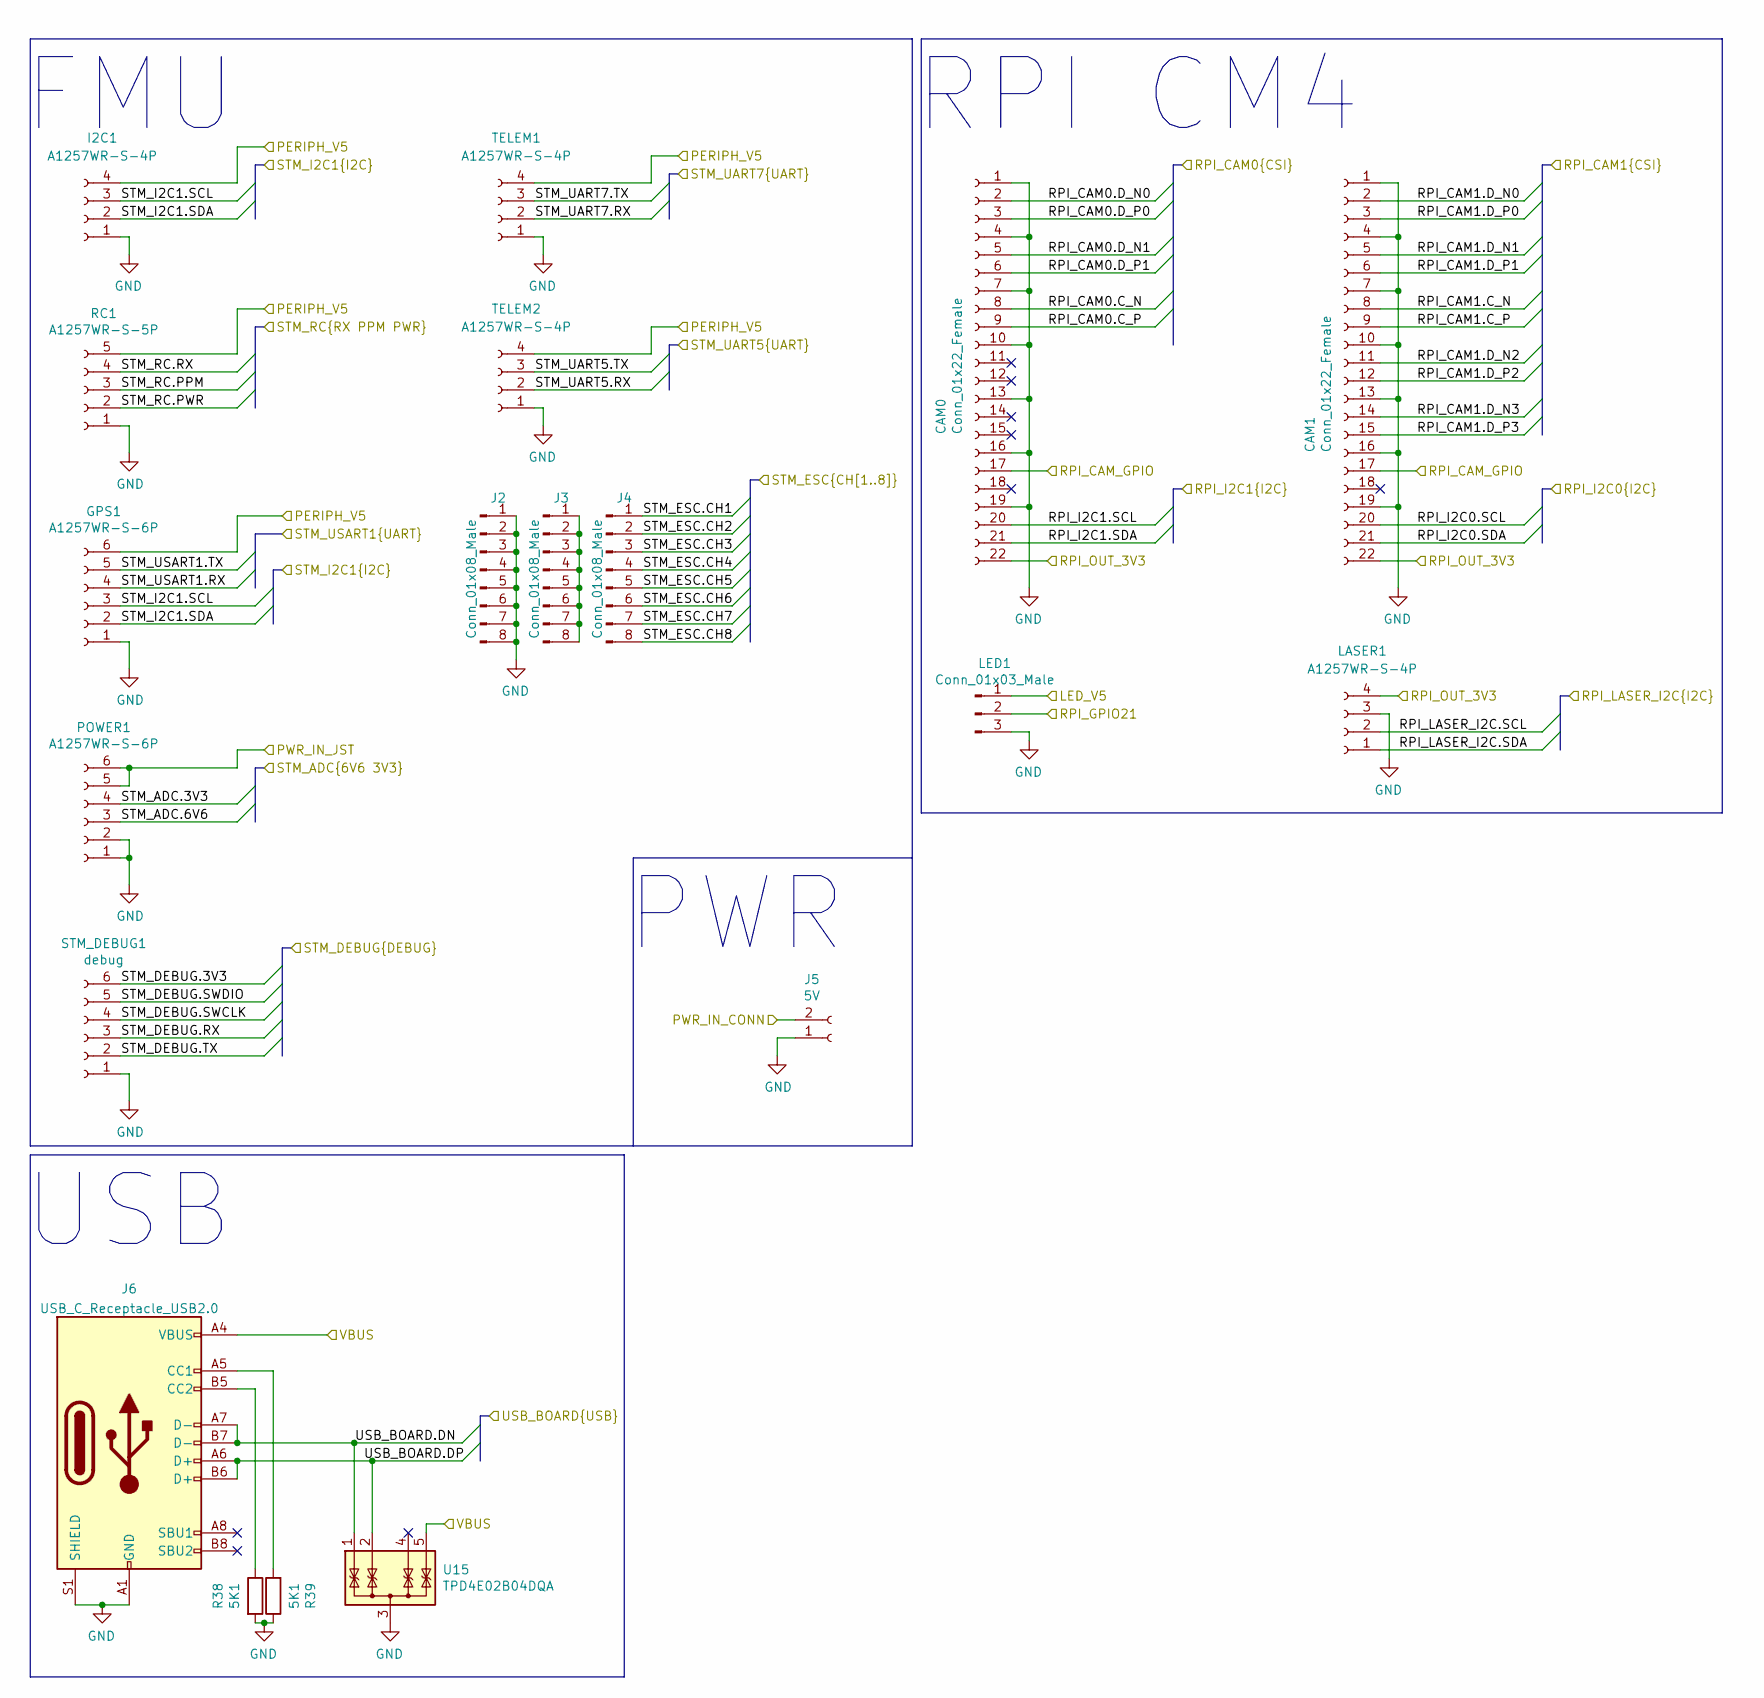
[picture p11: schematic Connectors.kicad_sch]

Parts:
CAM0, CAM1: Conn_01x22_Female; Hirose_FH12-22S-0.5SH_1x22-1MP_P0.50mm_Horizontal; Manufacturer_Part_Number AFC04-S22ECA-00
GPS1: A1257WR-S-6P; JST_GH_SM06B-GHS-TB_1x06-1MP_P1.25mm_Horizontal; Manufacturer_Part_Number A1257WR-S-6P
I2C1: A1257WR-S-4P; JST_GH_SM04B-GHS-TB_1x04-1MP_P1.25mm_Horizontal; Manufacturer_Part_Number A1257WR-S-4P
J2, J3, J4: Conn_01x08_Male; PinHeader_1x08_P2.54mm_Vertical
J5: 5V; power_pad; Manufacturer_Part_Number XT30U-M
J6: USB_C_Receptacle_USB2.0; USB_C_Receptacle_HRO_TYPE-C-31-M-12; Manufacturer_Part_Number 918-418K2023S40001
LASER1: A1257WR-S-4P; JST_GH_SM04B-GHS-TB_1x04-1MP_P1.25mm_Horizontal; Manufacturer_Part_Number A1257WR-S-4P
LED1: Conn_01x03_Male; PinHeader_1x03_P2.54mm_Vertical
POWER1: A1257WR-S-6P; JST_GH_SM06B-GHS-TB_1x06-1MP_P1.25mm_Horizontal; Manufacturer_Part_Number A1257WR-S-6P
R38, R39: 5K1; R_0402_1005Metric
RC1: A1257WR-S-5P; JST_GH_SM05B-GHS-TB_1x05-1MP_P1.25mm_Horizontal; Manufacturer_Part_Number A1257WR-S-5P
STM_DEBUG1: debug; debug_port
TELEM1, TELEM2: A1257WR-S-4P; JST_GH_SM04B-GHS-TB_1x04-1MP_P1.25mm_Horizontal; Manufacturer_Part_Number A1257WR-S-4P
U15: TPD4E02B04DQA; USON-10_2.5x1.0mm_P0.5mm; Manufacturer_Part_Number TPD4E02B04DQA

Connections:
/Connectors/LED_V5: J5.2, LED1.1; also elsewhere on the board
/Connectors/PWR_IN_JST: POWER1.5, POWER1.6; also elsewhere on the board
/Connectors/RPI_CAM0.C_N: CAM0.8; also elsewhere on the board
/Connectors/RPI_CAM0.C_P: CAM0.9; also elsewhere on the board
/Connectors/RPI_CAM0.D_N0: CAM0.2; also elsewhere on the board
/Connectors/RPI_CAM0.D_N1: CAM0.5; also elsewhere on the board
/Connectors/RPI_CAM0.D_P0: CAM0.3; also elsewhere on the board
/Connectors/RPI_CAM0.D_P1: CAM0.6; also elsewhere on the board
/Connectors/RPI_CAM1.C_N: CAM1.8; also elsewhere on the board
/Connectors/RPI_CAM1.C_P: CAM1.9; also elsewhere on the board
/Connectors/RPI_CAM1.D_N0: CAM1.2; also elsewhere on the board
/Connectors/RPI_CAM1.D_N1: CAM1.5; also elsewhere on the board
/Connectors/RPI_CAM1.D_N2: CAM1.11; also elsewhere on the board
/Connectors/RPI_CAM1.D_N3: CAM1.14; also elsewhere on the board
/Connectors/RPI_CAM1.D_P0: CAM1.3; also elsewhere on the board
/Connectors/RPI_CAM1.D_P1: CAM1.6; also elsewhere on the board
/Connectors/RPI_CAM1.D_P2: CAM1.12; also elsewhere on the board
/Connectors/RPI_CAM1.D_P3: CAM1.15; also elsewhere on the board
/Connectors/RPI_CAM_GPIO: CAM0.17, CAM1.17; also elsewhere on the board
/Connectors/RPI_GPIO21: LED1.2; also elsewhere on the board
/Connectors/RPI_I2C0.SDA: CAM1.21; also elsewhere on the board
/Connectors/RPI_I2C1.SDA: CAM0.21; also elsewhere on the board
/Connectors/RPI_LASER_I2C.SCL: LASER1.2; also elsewhere on the board
/Connectors/RPI_LASER_I2C.SDA: LASER1.1; also elsewhere on the board
/Connectors/RPI_OUT_3V3: CAM0.22, CAM1.22, LASER1.4; also elsewhere on the board
/Connectors/STM_ADC.3V3: POWER1.4; also elsewhere on the board
/Connectors/STM_ADC.6V6: POWER1.3; also elsewhere on the board
/Connectors/STM_DEBUG.3V3: STM_DEBUG1.6; also elsewhere on the board
/Connectors/STM_DEBUG.RX: STM_DEBUG1.3; also elsewhere on the board
/Connectors/STM_DEBUG.SWCLK: STM_DEBUG1.4; also elsewhere on the board
/Connectors/STM_DEBUG.SWDIO: STM_DEBUG1.5; also elsewhere on the board
/Connectors/STM_DEBUG.TX: STM_DEBUG1.2; also elsewhere on the board
/Connectors/STM_ESC.CH1: J4.1; also elsewhere on the board
/Connectors/STM_ESC.CH2: J4.2; also elsewhere on the board
/Connectors/STM_ESC.CH3: J4.3; also elsewhere on the board
/Connectors/STM_ESC.CH4: J4.4; also elsewhere on the board
/Connectors/STM_ESC.CH5: J4.5; also elsewhere on the board
/Connectors/STM_ESC.CH6: J4.6; also elsewhere on the board
/Connectors/STM_ESC.CH7: J4.7; also elsewhere on the board
/Connectors/STM_ESC.CH8: J4.8; also elsewhere on the board
/Connectors/STM_I2C1.SCL: GPS1.3, I2C1.3; also elsewhere on the board
/Connectors/STM_I2C1.SDA: GPS1.2, I2C1.2; also elsewhere on the board
/Connectors/STM_RC.PPM: RC1.3; also elsewhere on the board
/Connectors/STM_RC.PWR: RC1.2
/Connectors/STM_RC.RX: RC1.4; also elsewhere on the board
/Connectors/STM_UART5.RX: TELEM2.2; also elsewhere on the board
/Connectors/STM_UART5.TX: TELEM2.3; also elsewhere on the board
/Connectors/STM_UART7.RX: TELEM1.2; also elsewhere on the board
/Connectors/STM_UART7.TX: TELEM1.3; also elsewhere on the board
/Connectors/STM_USART1.RX: GPS1.4; also elsewhere on the board
/Connectors/STM_USART1.TX: GPS1.5; also elsewhere on the board
/Connectors/USB_BOARD.DN: J6.A7 (D-), J6.B7 (D-), U15.1 (IO1); also elsewhere on the board
/Connectors/USB_BOARD.DP: J6.A6 (D+), J6.B6 (D+), U15.2 (IO2); also elsewhere on the board
/STM32/STM_USB.VBUS: J6.A4 (VBUS), J6.A9 (VBUS), J6.B4 (VBUS), J6.B9 (VBUS), U15.5 (IO4); also elsewhere on the board
GND: CAM0.1, CAM0.4, CAM0.7, CAM0.10, CAM0.13, CAM0.16, CAM0.19, CAM0.MP, CAM1.1, CAM1.4, CAM1.7, CAM1.10, CAM1.13, CAM1.16, CAM1.19, GPS1.1, GPS1.MP, I2C1.1, I2C1.MP, J2.1, J2.2, J2.3, J2.4, J2.5, J2.6, J2.7, J2.8, J5.1, J6.A1 (GND), J6.A12 (GND), J6.B1 (GND), J6.B12 (GND), J6.S1 (SHIELD), LASER1.3, LASER1.MP, LED1.3, POWER1.1, POWER1.2, POWER1.MP, R38.2, R39.1, RC1.1, RC1.MP, STM_DEBUG1.1, TELEM1.1, TELEM1.MP, TELEM2.1, TELEM2.MP, U15.3 (G), U15.8 (G); also elsewhere on the board
unnamed: J3.1, J3.2, J3.3, J3.4, J3.5, J3.6, J3.7, J3.8
unnamed: J6.A5 (CC1), R39.2
unnamed: J6.B5 (CC2), R38.1
VCC: GPS1.6, I2C1.4, RC1.5, TELEM1.4, TELEM2.4; also elsewhere on the board

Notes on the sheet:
USB
RPI CM4
FMU
PWR

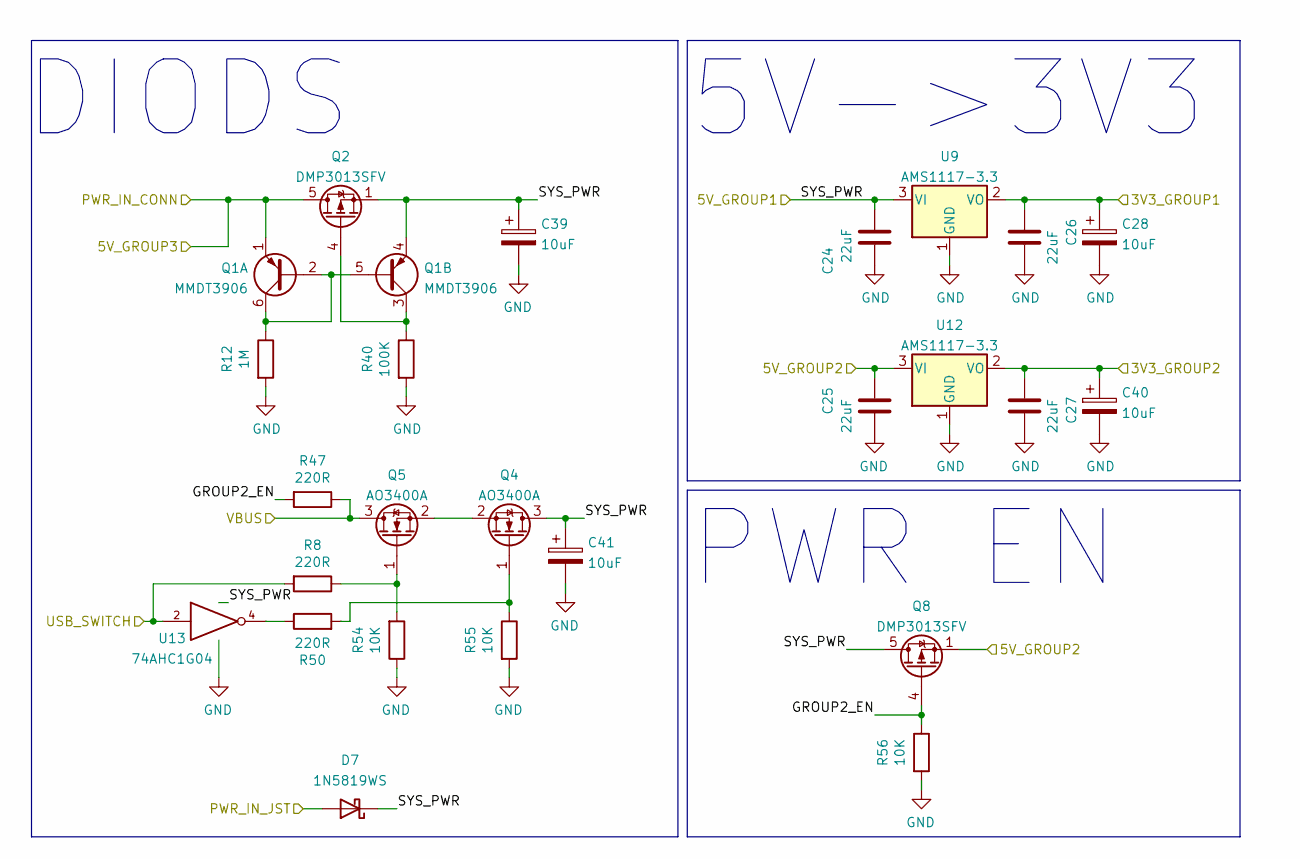
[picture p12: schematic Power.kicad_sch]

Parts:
C24, C25, C26, C27: 22uF; C_0402_1005Metric
C28, C39, C40, C41: 10uF; CP_EIA-3216-18_Kemet-A; Manufacturer_Part_Number CL31A226KAHNNNE
D7: 1N5819WS; D_SOD-323; Manufacturer_Part_Number 1N5819WS
Q1: MMDT3906; SOT-363_SC-70-6; Manufacturer_Part_Number MMDT3906
Q2: DMP3013SFV; Diodes_PowerDI3333-8; Manufacturer_Part_Number DMP3013SFV
Q4, Q5: AO3400A; SOT-23; Manufacturer_Part_Number AO3400A
Q8: DMP3013SFV; Diodes_PowerDI3333-8
R8, R47, R50: 220R; R_0402_1005Metric
R12: 1M; R_0402_1005Metric
R40: 100K; R_0402_1005Metric
R54, R55, R56: 10K; R_0402_1005Metric
U9, U12: AMS1117-3.3; SOT-223-3_TabPin2; Manufacturer_Part_Number AMS1117-3.3
U13: 74AHC1G04; SOT-353_SC-70-5; Manufacturer_Part_Number U74AHC1G04G-AL5-R

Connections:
/Connectors/LED_V5: Q1.1 (E1), Q2.5 (D); also elsewhere on the board
/Connectors/PWR_IN_JST: D7.2 (A); also elsewhere on the board
/ESP32/ESP_3V3: C27.1, C40.1, U12.2 (VO); also elsewhere on the board
/Power/3V3_GROUP1: C26.1, C28.1, U9.2 (VO); also elsewhere on the board
/Power/5V_GROUP2: C25.1, Q8.1 (S), Q8.2 (S), Q8.3 (S), U12.3 (VI); also elsewhere on the board
/Power/GROUP2_EN: Q8.4 (G), R47.2, R56.1
/RPi_CM4/RPI_USB.ID: R8.2, U13.2; also elsewhere on the board
/STM32/STM_USB.VBUS: Q5.3 (D), R47.1; also elsewhere on the board
GND: C24.1, C25.2, C26.2, C27.2, C28.2, C39.2, C40.2, C41.2, R12.2, R40.2, R54.1, R55.2, R56.2, U9.1 (GND), U12.1 (GND), U13.3 (GND); also elsewhere on the board
unnamed: Q1.2 (B1), Q1.5 (B2), Q1.6 (C1), R12.1
unnamed: Q1.3 (C2), Q2.4 (G), R40.1
unnamed: Q4.1 (G), R50.2, R55.1
unnamed: Q4.2 (S), Q5.2 (S)
unnamed: Q5.1 (G), R8.1, R54.2
unnamed: R50.1, U13.4
VCC: C24.2, C39.1, C41.1, D7.1 (K), Q1.4 (E2), Q2.1 (S), Q2.2 (S), Q2.3 (S), Q4.3 (D), Q8.5 (D), U9.3 (VI), U13.5 (VCC); also elsewhere on the board

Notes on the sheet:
DIODS
PWR EN
5V->3V3

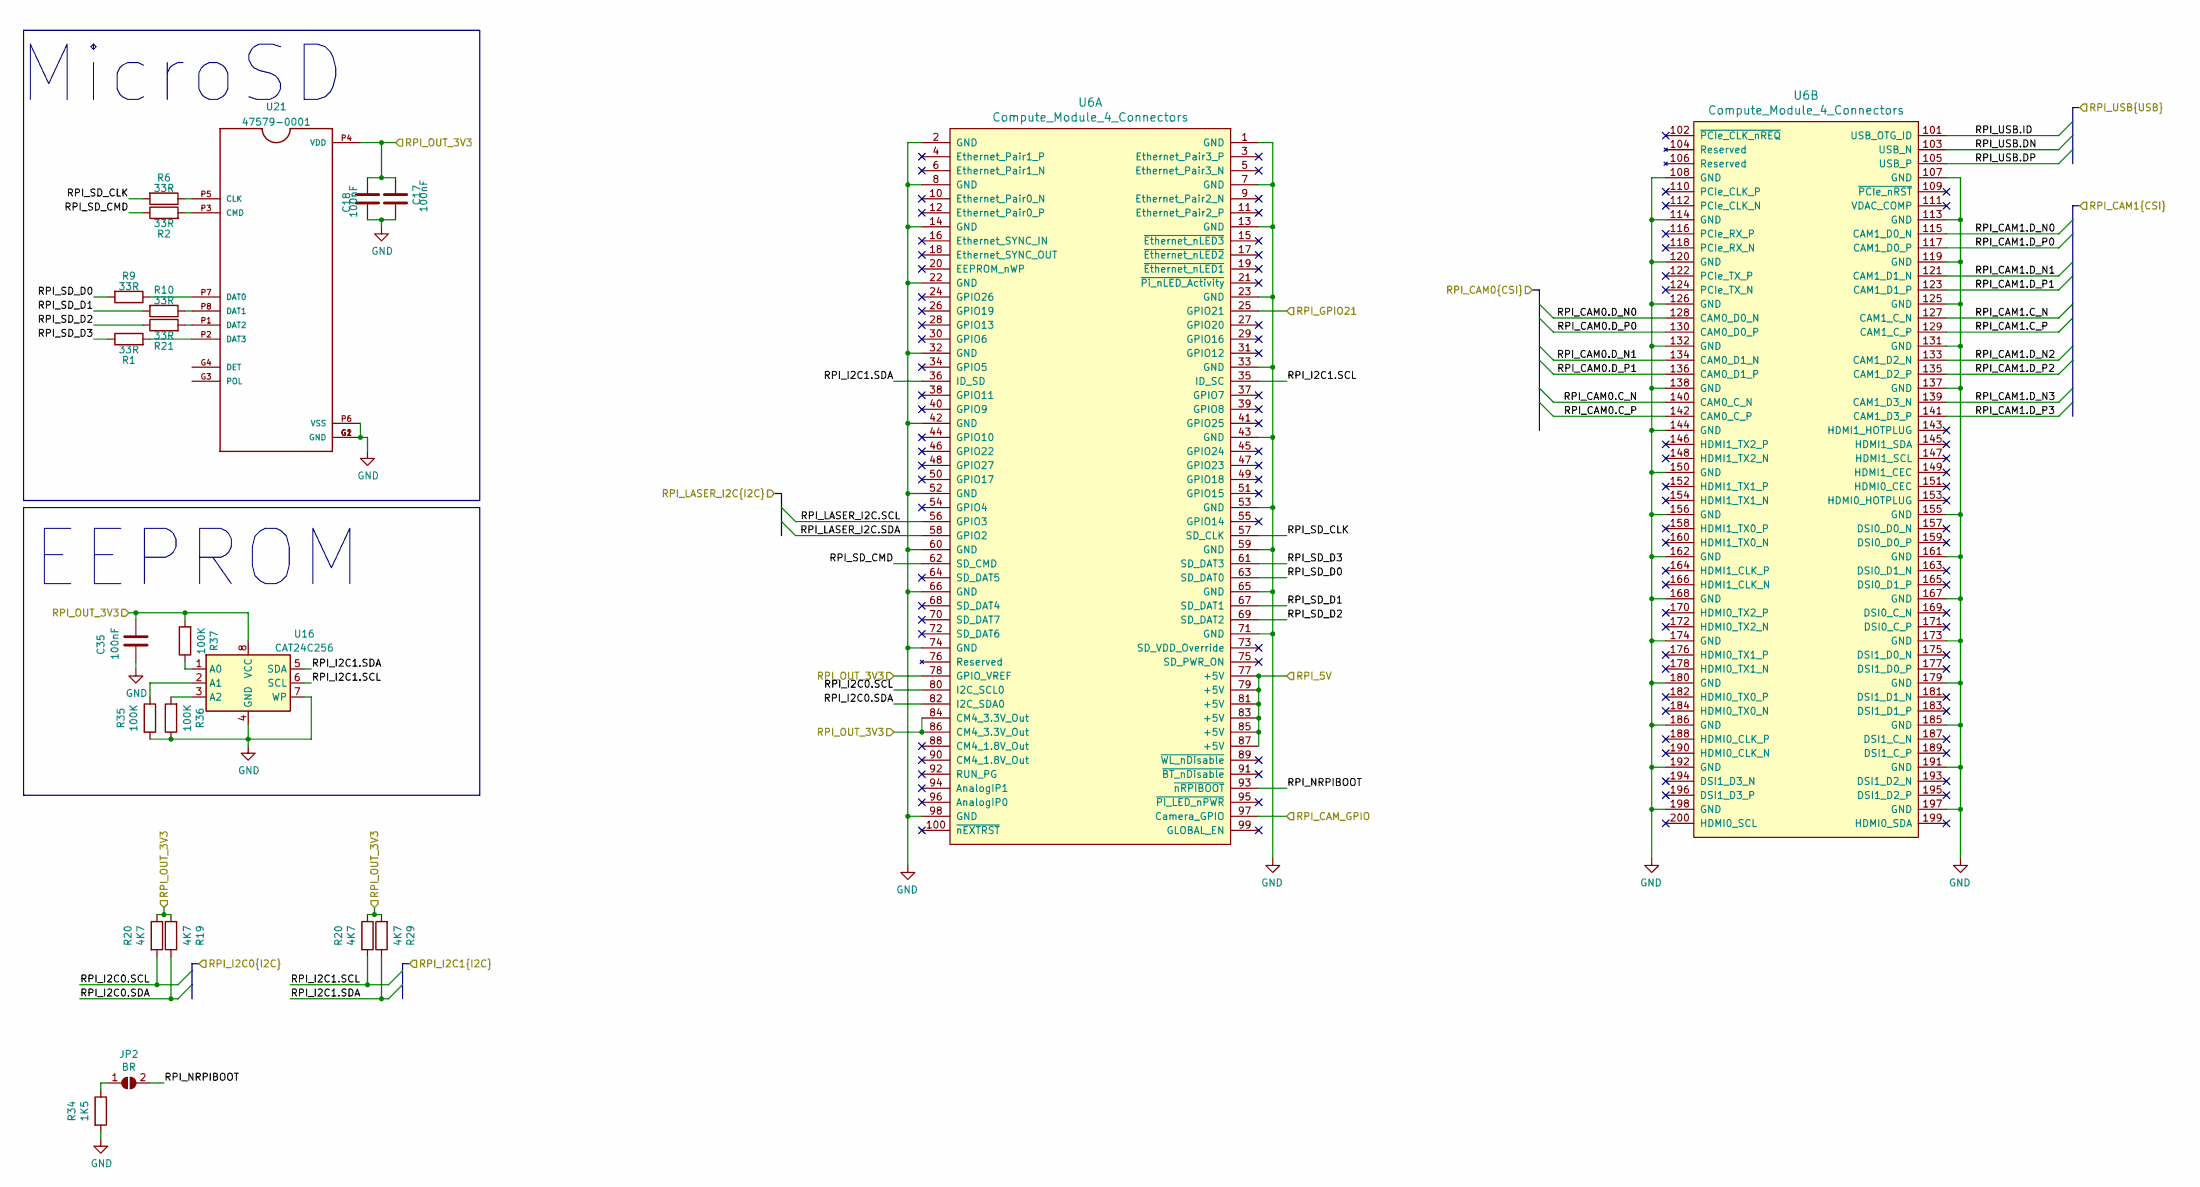
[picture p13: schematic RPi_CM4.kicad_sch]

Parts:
C17, C18, C35: 100nF; C_0402_1005Metric
JP2: BR; SolderJumper-2_P1.3mm_Open_TrianglePad1.0x1.5mm
R1, R2, R6, R9, R10, R21: 33R; R_0402_1005Metric
R19, R29: 4K7; R_0402_1005Metric
R20: 4.7K; R_0402_1005Metric
R34: 1K5; R_0402_1005Metric
R35, R36, R37: 100K; R_0402_1005Metric
U6: Compute_Module_4_Connectors; Raspberry-Pi-4-Compute-Module; Manufacturer_Part_Number DF40HC(3.0)-100DS-0.4V
U16: CAT24C256; DFN-8-1EP_3x2mm_P0.5mm_EP1.3x1.5mm; Manufacturer_Part_Number CAT24C256HU4IGT3
U21: 47579-0001; POS-8; Manufacturer_Part_Number TF-021B-H265

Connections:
/Connectors/RPI_CAM0.C_N: U6.140 (CAM0_C_N); also elsewhere on the board
/Connectors/RPI_CAM0.C_P: U6.142 (CAM0_C_P); also elsewhere on the board
/Connectors/RPI_CAM0.D_N0: U6.128 (CAM0_D0_N); also elsewhere on the board
/Connectors/RPI_CAM0.D_N1: U6.134 (CAM0_D1_N); also elsewhere on the board
/Connectors/RPI_CAM0.D_P0: U6.130 (CAM0_D0_P); also elsewhere on the board
/Connectors/RPI_CAM0.D_P1: U6.136 (CAM0_D1_P); also elsewhere on the board
/Connectors/RPI_CAM1.C_N: U6.127 (CAM1_C_N); also elsewhere on the board
/Connectors/RPI_CAM1.C_P: U6.129 (CAM1_C_P); also elsewhere on the board
/Connectors/RPI_CAM1.D_N0: U6.115 (CAM1_D0_N); also elsewhere on the board
/Connectors/RPI_CAM1.D_N1: U6.121 (CAM1_D1_N); also elsewhere on the board
/Connectors/RPI_CAM1.D_N2: U6.133 (CAM1_D2_N); also elsewhere on the board
/Connectors/RPI_CAM1.D_N3: U6.139 (CAM1_D3_N); also elsewhere on the board
/Connectors/RPI_CAM1.D_P0: U6.117 (CAM1_D0_P); also elsewhere on the board
/Connectors/RPI_CAM1.D_P1: U6.123 (CAM1_D1_P); also elsewhere on the board
/Connectors/RPI_CAM1.D_P2: U6.135 (CAM1_D2_P); also elsewhere on the board
/Connectors/RPI_CAM1.D_P3: U6.141 (CAM1_D3_P); also elsewhere on the board
/Connectors/RPI_CAM_GPIO: U6.97 (Camera_GPIO); also elsewhere on the board
/Connectors/RPI_GPIO21: U6.25 (GPIO21); also elsewhere on the board
/Connectors/RPI_I2C0.SDA: R19.1, U6.82 (I2C_SDA0); also elsewhere on the board
/Connectors/RPI_I2C1.SDA: R29.1, U6.36 (ID_SD), U16.5 (SDA); also elsewhere on the board
/Connectors/RPI_LASER_I2C.SCL: U6.56 (GPIO3); also elsewhere on the board
/Connectors/RPI_LASER_I2C.SDA: U6.58 (GPIO2); also elsewhere on the board
/Connectors/RPI_OUT_3V3: C17.1, C18.2, C35.2, R19.2, R20.1, R29.2, R37.2, U6.78 (GPIO_VREF), U6.84 (CM4_3.3V_Out), U6.86 (CM4_3.3V_Out), U16.8 (VCC), U21.P4 (VDD); also elsewhere on the board
/Power/5V_GROUP2: U6.77 (+5V), U6.79 (+5V), U6.81 (+5V), U6.83 (+5V), U6.85 (+5V), U6.87 (+5V); also elsewhere on the board
/RPi_CM4/RPI_NRPIBOOT: JP2.2 (B), U6.93 (~nRPIBOOT)
/RPi_CM4/RPI_SD_CLK: R6.2, U6.57 (SD_CLK)
/RPi_CM4/RPI_SD_CMD: R2.1, U6.62 (SD_CMD)
/RPi_CM4/RPI_SD_D0: R9.2, U6.63 (SD_DAT0)
/RPi_CM4/RPI_SD_D1: R10.2, U6.67 (SD_DAT1)
/RPi_CM4/RPI_SD_D2: R21.1, U6.69 (SD_DAT2)
/RPi_CM4/RPI_SD_D3: R1.1, U6.61 (SD_DAT3)
/RPi_CM4/RPI_USB.DN: U6.103 (USB_N); also elsewhere on the board
/RPi_CM4/RPI_USB.DP: U6.105 (USB_P); also elsewhere on the board
/RPi_CM4/RPI_USB.ID: U6.101 (USB_OTG_ID); also elsewhere on the board
GND: C17.2, C18.1, C35.1, R34.2, R35.2, R36.1, U6.1 (GND), U6.2 (GND), U6.7 (GND), U6.8 (GND), U6.13 (GND), U6.14 (GND), U6.22 (GND), U6.23 (GND), U6.32 (GND), U6.33 (GND), U6.42 (GND), U6.43 (GND), U6.52 (GND), U6.53 (GND), U6.59 (GND), U6.60 (GND), U6.65 (GND), U6.66 (GND), U6.71 (GND), U6.74 (GND), U6.98 (GND), U6.107 (GND), U6.108 (GND), U6.113 (GND), U6.114 (GND), U6.119 (GND), U6.120 (GND), U6.125 (GND), U6.126 (GND), U6.131 (GND), U6.132 (GND), U6.137 (GND), U6.138 (GND), U6.144 (GND), U6.150 (GND), U6.155 (GND), U6.156 (GND), U6.161 (GND), U6.162 (GND), U6.167 (GND), U6.168 (GND), U6.173 (GND), U6.174 (GND), U6.179 (GND), U6.180 (GND), U6.185 (GND), U6.186 (GND), U6.191 (GND), U6.192 (GND), U6.197 (GND), U6.198 (GND), U16.4 (GND), U16.7 (WP), U21.G1 (GND), U21.G2 (GND), U21.P6 (VSS); also elsewhere on the board
unnamed: JP2.1 (A), R34.1
unnamed: R1.2, U21.P2 (DAT3)
unnamed: R2.2, U21.P3 (CMD)
unnamed: R6.1, U21.P5 (CLK)
unnamed: R9.1, U21.P7 (DAT0)
unnamed: R10.1, U21.P8 (DAT1)
unnamed: R21.2, U21.P1 (DAT2)
unnamed: R35.1, U16.2 (A1)
unnamed: R36.2, U16.3 (A2)
unnamed: R37.1, U16.1 (A0)

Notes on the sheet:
EEPROM
MicroSD

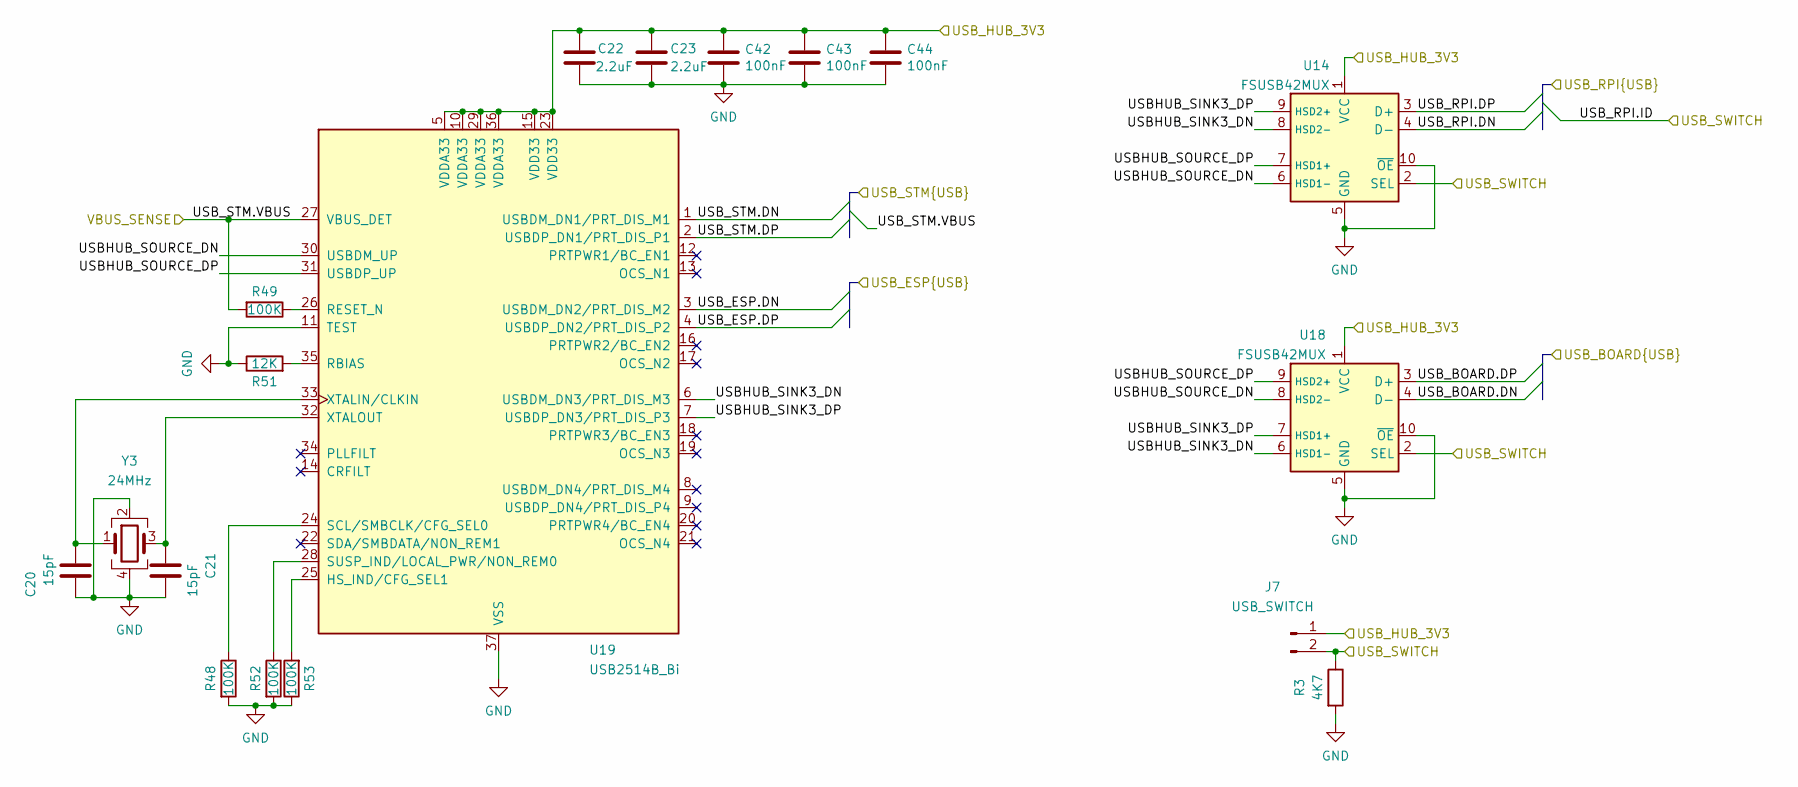
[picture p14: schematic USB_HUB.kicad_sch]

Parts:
C20, C21: 15pF; C_0402_1005Metric
C22, C23: 2.2uF; C_0402_1005Metric
C42, C43, C44: 100nF; C_0402_1005Metric
J7: USB_SWITCH; PinHeader_1x02_P2.54mm_Vertical
R3: 4K7; R_0402_1005Metric
R48, R49, R52, R53: 100K; R_0402_1005Metric
R51: 12K; R_0402_1005Metric
U14, U18: FSUSB42MUX; UQFN-10_1.4x1.8mm_P0.4mm; Manufacturer_Part_Number FSUSB42UMX
U19: USB2514B_Bi; QFN-36-1EP_6x6mm_P0.5mm_EP3.7x3.7mm; Manufacturer_Part_Number USB2514B-AEZC-TR
Y3: 24MHz; Crystal_SMD_2016-4Pin_2.0x1.6mm; Manufacturer_Part_Number OT201624MJBA4SL

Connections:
/Connectors/USB_BOARD.DN: U18.4 (D-); also elsewhere on the board
/Connectors/USB_BOARD.DP: U18.3 (D+); also elsewhere on the board
/ESP32/ESP_3V3: C22.2, C23.1, C42.1, C43.1, C44.1, J7.1, U14.1 (VCC), U18.1 (VCC), U19.5 (VDDA33), U19.10 (VDDA33), U19.15 (VDD33), U19.23 (VDD33), U19.29 (VDDA33), U19.36 (VDDA33); also elsewhere on the board
/ESP32/ESP_USB.DN: U19.3 (USBDM_DN2/PRT_DIS_M2); also elsewhere on the board
/ESP32/ESP_USB.DP: U19.4 (USBDP_DN2/PRT_DIS_P2); also elsewhere on the board
/RPi_CM4/RPI_USB.DN: U14.4 (D-); also elsewhere on the board
/RPi_CM4/RPI_USB.DP: U14.3 (D+); also elsewhere on the board
/RPi_CM4/RPI_USB.ID: J7.2, R3.1, U14.2 (SEL), U18.2 (SEL); also elsewhere on the board
/STM32/STM_USB.DN: U19.1 (USBDM_DN1/PRT_DIS_M1); also elsewhere on the board
/STM32/STM_USB.DP: U19.2 (USBDP_DN1/PRT_DIS_P1); also elsewhere on the board
/STM32/STM_USB.VBUS: R49.2, U19.27 (VBUS_DET); also elsewhere on the board
/USB_HUB/USBHUB_SINK3_DN: U14.8 (HSD2-), U18.6 (HSD1-), U19.6 (USBDM_DN3/PRT_DIS_M3)
/USB_HUB/USBHUB_SINK3_DP: U14.9 (HSD2+), U18.7 (HSD1+), U19.7 (USBDP_DN3/PRT_DIS_P3)
/USB_HUB/USBHUB_SOURCE_DN: U14.6 (HSD1-), U18.8 (HSD2-), U19.30 (USBDM_UP)
/USB_HUB/USBHUB_SOURCE_DP: U14.7 (HSD1+), U18.9 (HSD2+), U19.31 (USBDP_UP)
GND: C20.1, C21.2, C22.1, C23.2, C42.2, C43.2, C44.2, R3.2, R48.2, R51.1, R52.2, R53.1, U14.5 (GND), U14.10 (~OE), U18.5 (GND), U18.10 (~OE), U19.11 (TEST), U19.37 (VSS), Y3.2, Y3.4; also elsewhere on the board
unnamed: C20.2, U19.33 (XTALIN/CLKIN), Y3.1
unnamed: C21.1, U19.32 (XTALOUT), Y3.3
unnamed: R48.1, U19.24 (SCL/SMBCLK/CFG_SEL0)
unnamed: R49.1, U19.26 (RESET_N)
unnamed: R51.2, U19.35 (RBIAS)
unnamed: R52.1, U19.28 (SUSP_IND/LOCAL_PWR/NON_REM0)
unnamed: R53.2, U19.25 (HS_IND/CFG_SEL1)

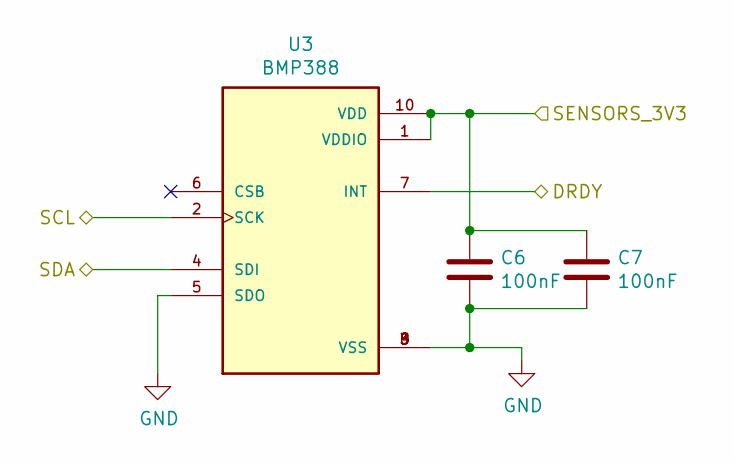
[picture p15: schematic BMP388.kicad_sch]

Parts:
C6, C7: 100nF; C_0402_1005Metric
U3: BMP388; PQFN50P200X200X80-10N; PARTREV 1.1

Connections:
/STM32/SENSORS_3V3: C6.1, C7.1, U3.1 (VDDIO), U3.10 (VDD); also elsewhere on the board
/STM32/STM_I2C4.DRDY1: U3.7 (INT); also elsewhere on the board
/STM32/STM_I2C4.SCL: U3.2 (SCK); also elsewhere on the board
/STM32/STM_I2C4.SDA: U3.4 (SDI); also elsewhere on the board
GND: C6.2, C7.2, U3.3 (VSS), U3.5 (SDO), U3.8 (VSS), U3.9 (VSS); also elsewhere on the board

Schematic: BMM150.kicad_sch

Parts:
C36, C37: 100nF; C_0402_1005Metric
R41: 10K; R_0402_1005Metric
U5: BMM150; WLCSP-12_1.56x1.56mm_P0.4mm; Manufacturer_Part_Number BMM150

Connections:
/STM32/SENSORS_3V3: C36.1, C37.1, R41.1, U5.B2 (VDDIO), U5.E5 (VDD); also elsewhere on the board
/STM32/STM_I2C4.DRDY2: U5.D4 (DRDY); also elsewhere on the board
/STM32/STM_I2C4.SCL: U5.A3 (SCK); also elsewhere on the board
/STM32/STM_I2C4.SDA: U5.B4 (SDI); also elsewhere on the board
GND: C36.2, C37.2, U5.A5 (CSB), U5.C1 (SDO), U5.C5 (GND), U5.E1 (GND), U5.E3 (GND); also elsewhere on the board
unnamed: R41.2, U5.A1 (PS)

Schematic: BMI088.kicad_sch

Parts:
C15, C16: 100nF; C_0402_1005Metric
U17: BMI088; PQFN50P450X300X100-16N; Manufacturer_Part_Number BMI088

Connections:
/STM32/SENSORS_3V3: C15.1, C16.1, U17.3 (VDD), U17.11 (VDDIO); also elsewhere on the board
/STM32/STM_SPI3.CS1: U17.14 (CSB1); also elsewhere on the board
/STM32/STM_SPI3.CS2: U17.5 (CSB2); also elsewhere on the board
/STM32/STM_SPI3.DRDY1: U17.16 (INT1); also elsewhere on the board
/STM32/STM_SPI3.DRDY2: U17.1 (INT2); also elsewhere on the board
/STM32/STM_SPI3.MISO: U17.10 (SDO2), U17.15 (SDO1); also elsewhere on the board
/STM32/STM_SPI3.MOSI: U17.9 (SDA/SDI); also elsewhere on the board
/STM32/STM_SPI3.SCK: U17.8 (SCL/SCK); also elsewhere on the board
GND: C15.2, C16.2, U17.2 (NC), U17.4 (GNDA), U17.6 (GNDIO), U17.7 (PS); also elsewhere on the board

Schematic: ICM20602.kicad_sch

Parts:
C3: 2.2uF; C_0402_1005Metric
C4, C5: 100nF; C_0402_1005Metric
U2: ICM-20602; LGA-16_3x3mm_P0.5mm_LayoutBorder3x5y; Manufacturer_Part_Number ICM-20602

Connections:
/STM32/SENSORS_3V3: C3.1, C5.1, U2.1 (VDDIO), U2.16 (VDD); also elsewhere on the board
/STM32/STM_SPI1.CS1: U2.5 (~CS); also elsewhere on the board
/STM32/STM_SPI1.DRDY1: U2.6 (INT); also elsewhere on the board
/STM32/STM_SPI1.MISO: U2.4 (SAO/SD0); also elsewhere on the board
/STM32/STM_SPI1.MOSI: U2.3 (SDA/SDI); also elsewhere on the board
/STM32/STM_SPI1.SCK: U2.2 (SCL/SPC); also elsewhere on the board
GND: C3.2, C4.2, C5.2, U2.8 (FSYNC), U2.9 (GND), U2.10 (GND), U2.11 (GND), U2.12 (GND), U2.13 (GND), U2.15 (GND); also elsewhere on the board
unnamed: C4.1, U2.14 (REGOUT)

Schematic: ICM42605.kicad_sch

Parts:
C13: 100nF; C_0402_1005Metric
C14: 2.2uF; C_0402_1005Metric
U7: ICM-42605; PQFN50P300X250X97-14N; PARTREV 0.4

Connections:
/STM32/SENSORS_3V3: C13.2, C14.1, U7.5 (VDDIO), U7.8 (VDD); also elsewhere on the board
/STM32/STM_SPI2.CS1: U7.12 (AP_CS); also elsewhere on the board
/STM32/STM_SPI2.DRDY2: U7.4 (INT1/INT); also elsewhere on the board
/STM32/STM_SPI2.MISO: U7.1 (AP_SDO/AP_ADO); also elsewhere on the board
/STM32/STM_SPI2.MOSI: U7.14 (AP_SDA/AP_SDIO/AP_SDI); also elsewhere on the board
/STM32/STM_SPI2.SCK: U7.13 (AP_SCL/AP_SCLK); also elsewhere on the board
GND: C13.1, C14.2, U7.2 (RESV_1), U7.3 (RESV_2), U7.6 (GND), U7.7 (RESV_3), U7.10 (RESV_4), U7.11 (RESV_5); also elsewhere on the board

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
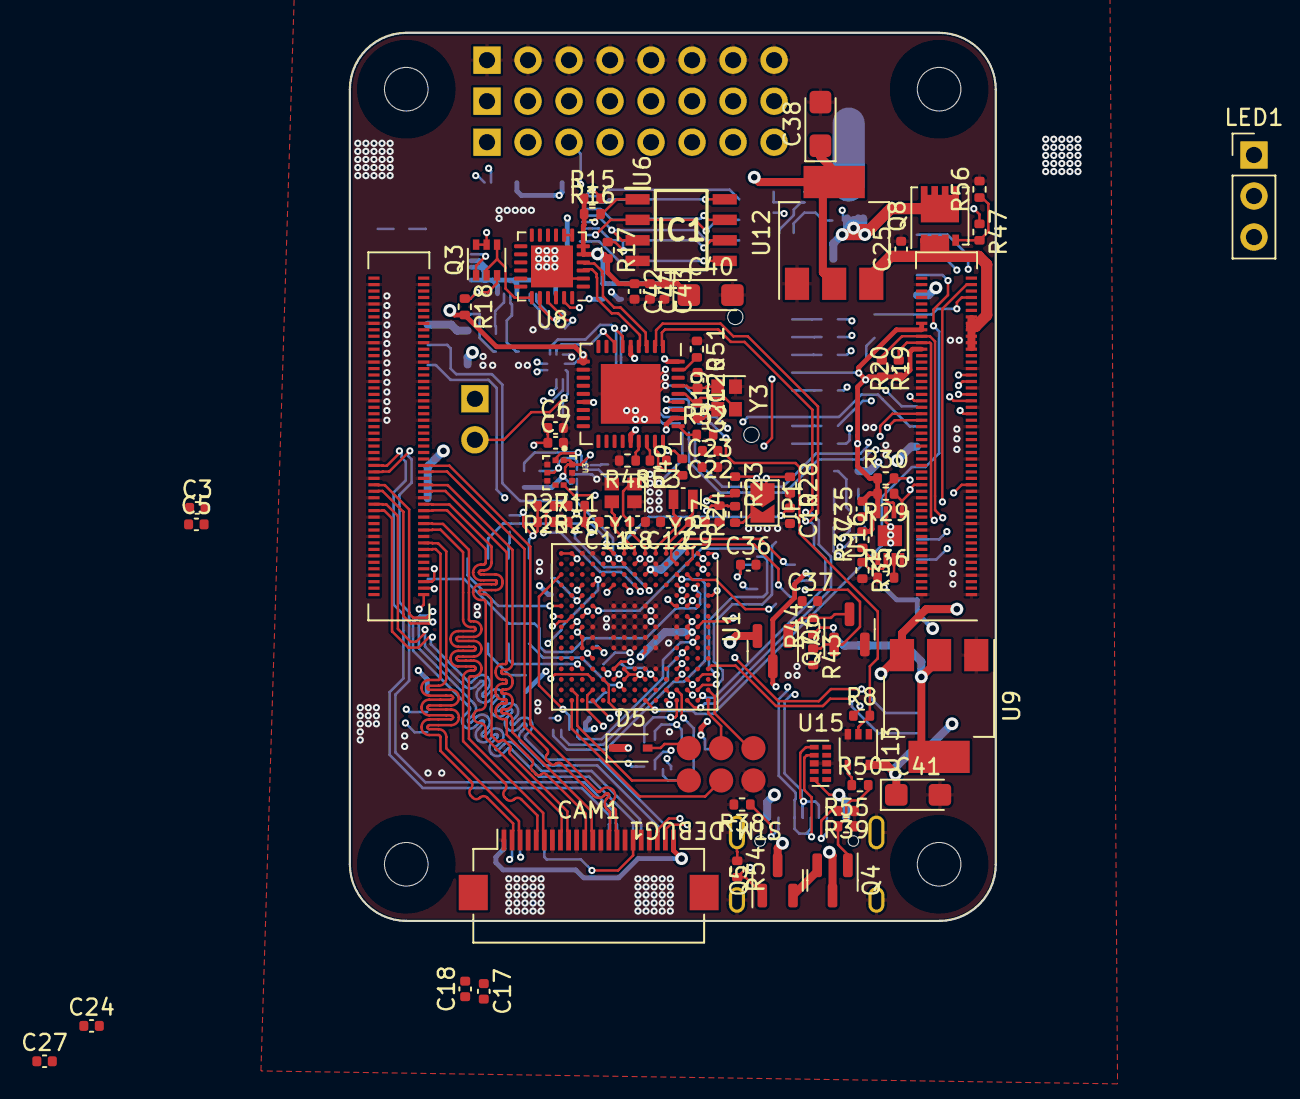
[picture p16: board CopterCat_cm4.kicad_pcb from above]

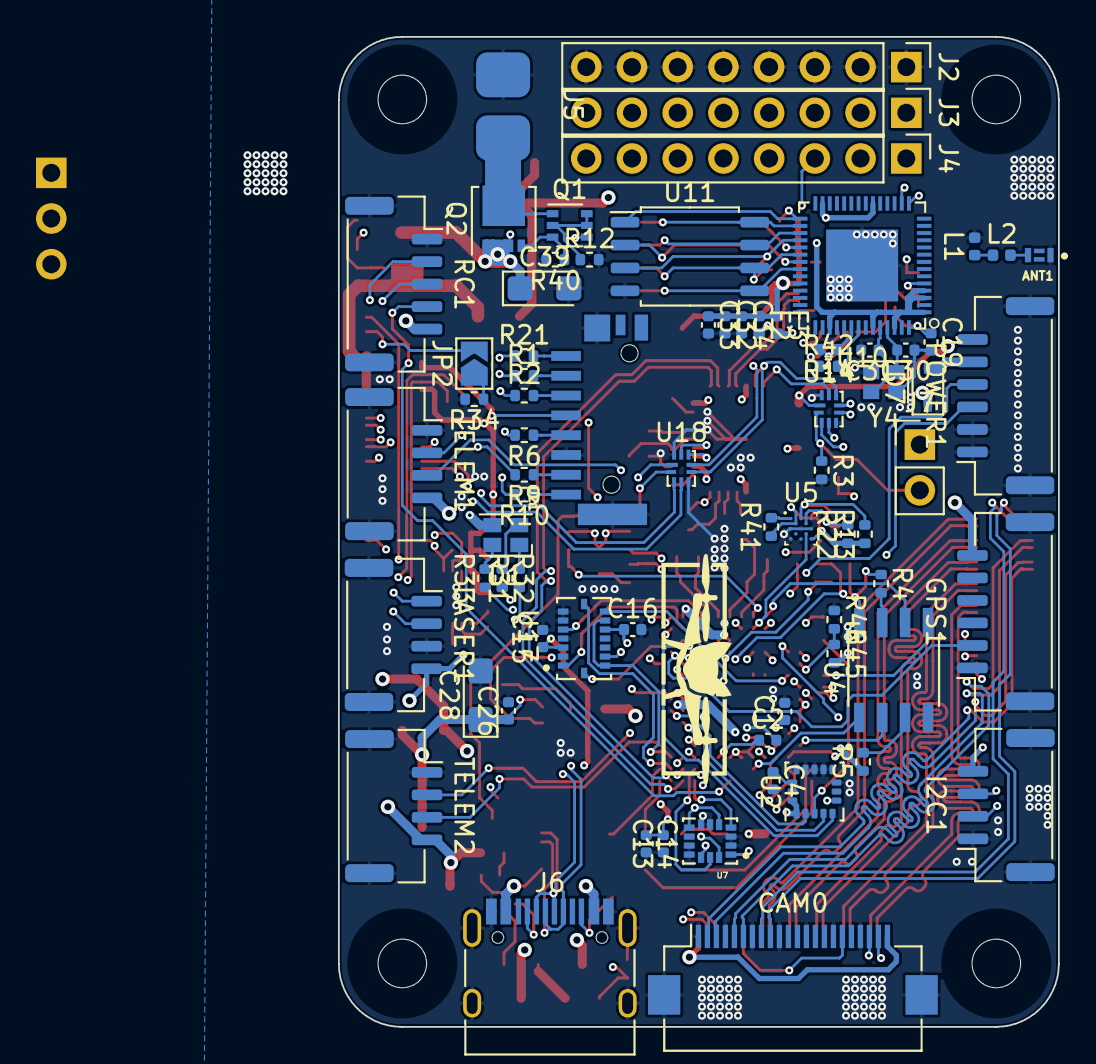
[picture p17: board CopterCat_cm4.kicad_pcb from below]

Board: 4 copper layers, 40.0 x 55.0 mm, 159 parts (73 on the bottom side), 182 nets.

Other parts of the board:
R20#2: 4.7K; R_0402_1005Metric

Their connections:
/Connectors/RPI_OUT_3V3: R20#2.1; also elsewhere on the board

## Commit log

2021-12-29 start adding usb-c
    [Connectors.sch, Power.sch, STM32.sch]
2022-01-02 start migrating to kicad v6
    [Connectors.sch, CopterCat_cm4.kicad_pcb, ESP32.sch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]
2022-01-27 доработка схемы + делаем красиво
    [BMI088.kicad_sch, BMM150.kicad_sch, BMP388.kicad_sch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]
2022-02-03 плата практически готова
    [Connectors.kicad_sch, CopterCat_cm4.kicad_pcb, CopterCat_cm4.kicad_sch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]
2022-02-03 продам гараж
    [Connectors.kicad_sch, CopterCat_cm4.kicad_pcb, CopterCat_cm4.kicad_sch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]
2022-02-04 autoroute test
    [CopterCat_cm4.kicad_pcb]
2022-02-05 тестирование
    [Connectors.kicad_sch, CopterCat_cm4.kicad_pcb, CopterCat_cm4.kicad_sch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]
2022-02-05 second version
    [CopterCat_cm4.kicad_pcb, ESP32.kicad_sch, STM32.kicad_sch]
2022-02-06 первый релиз
    [Connectors.kicad_sch, CopterCat_cm4.kicad_sch, STM32.kicad_sch]
2022-02-07 Теперь точно релиз
2022-02-07 Adding esp32 gpio pins
    [Connectors.kicad_sch, CopterCat_cm4.kicad_sch, ESP32.kicad_sch]
2022-02-08 Little fix
    [BMI088.kicad_sch, BMM150.kicad_sch, BMP388.kicad_sch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]
2022-02-13 little fix 2
    [CopterCat_cm4.kicad_sch]
2022-02-13 забыл сохранить
2022-03-01 First order
    [BMI088.kicad_sch, BMM150.kicad_sch, BMP388.kicad_sch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]
2022-04-23 аштфд
